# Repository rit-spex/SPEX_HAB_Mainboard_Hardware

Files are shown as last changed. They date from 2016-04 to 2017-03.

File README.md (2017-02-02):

# SPEX_HAB_Mainboard_Hardware

Mainboard for RIT SPEX's High Altitude Balloon Program. 
This board is part of a modular system that allows for quick reuse and testing of future cubesat payloads.

Hardware on board includes:
- Altimeter
- 9DOF IMU
- Temperature Sensor
- Three external Thermistors
- Onboard MicroSD Storage 
- MOSFETs for multiple voltages
- Full Dataline ESD Protection

   
 

   



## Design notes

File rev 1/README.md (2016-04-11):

# SPEX_HAB_Mainboard_Hardware

Mainboard for RIT SPEX's High Altitude Balloon Program. 
This board is part of a modular system that allows for quick reuse and testing of future cubesat payloads.

Hardware on board includes:
- Altimeter
- 9DOF IMU
- Temperature Sensor
- Three external Thermistors
- 64Mbit of Flash Storage
- Onboard MicroSD Storage 
- Relays and MOSFETs for multiple voltages
- Full Dataline ESD Protection

   
 

   



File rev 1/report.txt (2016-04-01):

Info: Reading netlist file "C:\Users\matthew\Desktop\SPEX-Mainboard-Hardware\Spex-Mainboard-Hardware.net".

Info: Using references to match components and footprints.

Info: Checking netlist component footprint "C1:/5657EA84:Capacitors_SMD:C_0603".

Adding new component "C1:/5657EA84" footprint "Capacitors_SMD:C_0603".

Changing component "C1:/5657EA84" pin "1" net name from "" to "+3V3".

Changing component "C1:/5657EA84" pin "2" net name from "" to "GND".

Info: Checking netlist component footprint "C2:/5657EA4F:Capacitors_SMD:C_0603".

Adding new component "C2:/5657EA4F" footprint "Capacitors_SMD:C_0603".

Changing component "C2:/5657EA4F" pin "1" net name from "" to "+3V3".

Changing component "C2:/5657EA4F" pin "2" net name from "" to "GND".

Info: Checking netlist component footprint "C3:/5657C82F:Capacitors_SMD:C_0603".

Adding new component "C3:/5657C82F" footprint "Capacitors_SMD:C_0603".

Changing component "C3:/5657C82F" pin "1" net name from "" to "+3V3".

Changing component "C3:/5657C82F" pin "2" net name from "" to "GND".

Info: Checking netlist component footprint "C4:/5657C7F2:Capacitors_SMD:C_0603".

Adding new component "C4:/5657C7F2" footprint "Capacitors_SMD:C_0603".

Changing component "C4:/5657C7F2" pin "1" net name from "" to "+3V3".

Changing component "C4:/5657C7F2" pin "2" net name from "" to "GND".

Info: Checking netlist component footprint "C5:/5700DE6B:Capacitors_SMD:C_0603".

Adding new component "C5:/5700DE6B" footprint "Capacitors_SMD:C_0603".

Changing component "C5:/5700DE6B" pin "1" net name from "" to "+3V3".

Changing component "C5:/5700DE6B" pin "2" net name from "" to "GND".

Info: Checking netlist component footprint "C6:/56FA860A:Capacitors_SMD:C_0603".

Adding new component "C6:/56FA860A" footprint "Capacitors_SMD:C_0603".

Changing component "C6:/56FA860A" pin "1" net name from "" to "Net-(C6-Pad1)".

Changing component "C6:/56FA860A" pin "2" net name from "" to "GND".

Info: Checking netlist component footprint "C7:/5679E0BF:Capacitors_SMD:C_0603".

Adding new component "C7:/5679E0BF" footprint "Capacitors_SMD:C_0603".

Changing component "C7:/5679E0BF" pin "1" net name from "" to "Net-(C7-Pad1)".

Changing component "C7:/5679E0BF" pin "2" net name from "" to "GND".

Info: Checking netlist component footprint "C8:/5679E124:Capacitors_SMD:C_0603".

Adding new component "C8:/5679E124" footprint "Capacitors_SMD:C_0603".

Changing component "C8:/5679E124" pin "1" net name from "" to "Net-(C8-Pad1)".

Changing component "C8:/5679E124" pin "2" net name from "" to "GND".

Info: Checking netlist component footprint "C9:/56DF35A9/56DF43E0:Capacitors_SMD:C_0603".

Adding new component "C9:/56DF35A9/56DF43E0" footprint "Capacitors_SMD:C_0603".

Changing component "C9:/56DF35A9/56DF43E0" pin "1" net name from "" to "Net-(C9-Pad1)".

Changing component "C9:/56DF35A9/56DF43E0" pin "2" net name from "" to "GND".

Info: Checking netlist component footprint "C10:/56DF35A9/56DF438F:Capacitors_SMD:C_0603".

Adding new component "C10:/56DF35A9/56DF438F" footprint "Capacitors_SMD:C_0603".

Changing component "C10:/56DF35A9/56DF438F" pin "1" net name from "" to "+3V3".

Changing component "C10:/56DF35A9/56DF438F" pin "2" net name from "" to "GND".

Info: Checking netlist component footprint "C11:/56DF35A9/56DF6921:Capacitors_SMD:C_0603".

Adding new component "C11:/56DF35A9/56DF6921" footprint "Capacitors_SMD:C_0603".

Changing component "C11:/56DF35A9/56DF6921" pin "1" net name from "" to "+3V3".

Changing component "C11:/56DF35A9/56DF6921" pin "2" net name from "" to "GND".

Info: Checking netlist component footprint "C12:/56DF35A9/56DF6AFC:Capacitors_SMD:C_0603".

Adding new component "C12:/56DF35A9/56DF6AFC" footprint "Capacitors_SMD:C_0603".

Changing component "C12:/56DF35A9/56DF6AFC" pin "1" net name from "" to "Net-(C12-Pad1)".

Changing component "C12:/56DF35A9/56DF6AFC" pin "2" net name from "" to "GND".

Info: Checking netlist component footprint "C13:/56DF35A9/56DF6B56:Capacitors_SMD:C_0603".

Adding new component "C13:/56DF35A9/56DF6B56" footprint "Capacitors_SMD:C_0603".

Changing component "C13:/56DF35A9/56DF6B56" pin "1" net name from "" to "Net-(C13-Pad1)".

Changing component "C13:/56DF35A9/56DF6B56" pin "2" net name from "" to "GND".

Info: Checking netlist component footprint "C14:/56DF35A9/56E7C20E:Capacitors_SMD:C_0603".

Adding new component "C14:/56DF35A9/56E7C20E" footprint "Capacitors_SMD:C_0603".

Changing component "C14:/56DF35A9/56E7C20E" pin "1" net name from "" to "/HAB Sensors/2.5VRefVoltage".

Changing component "C14:/56DF35A9/56E7C20E" pin "2" net name from "" to "GND".

Info: Checking netlist component footprint "C15:/56DF35A9/56DF6C79:Capacitors_SMD:C_0603".

Adding new component "C15:/56DF35A9/56DF6C79" footprint "Capacitors_SMD:C_0603".

Changing component "C15:/56DF35A9/56DF6C79" pin "1" net name from "" to "+3V3".

Changing component "C15:/56DF35A9/56DF6C79" pin "2" net name from "" to "GND".

Info: Checking netlist component footprint "C16:/56DF35A9/56DF6DC2:Capacitors_SMD:C_0603".

Adding new component "C16:/56DF35A9/56DF6DC2" footprint "Capacitors_SMD:C_0603".

Changing component "C16:/56DF35A9/56DF6DC2" pin "1" net name from "" to "+3V3".

Changing component "C16:/56DF35A9/56DF6DC2" pin "2" net name from "" to "GND".

Info: Checking netlist component footprint "C17:/56EB0DA0/56EC0199:Capacitors_SMD:C_0603".

Adding new component "C17:/56EB0DA0/56EC0199" footprint "Capacitors_SMD:C_0603".

Changing component "C17:/56EB0DA0/56EC0199" pin "1" net name from "" to "+3V3".

Changing component "C17:/56EB0DA0/56EC0199" pin "2" net name from "" to "GND".

Info: Checking netlist component footprint "C18:/56EB0DA0/56EB2C07:Capacitors_SMD:C_0603".

Adding new component "C18:/56EB0DA0/56EB2C07" footprint "Capacitors_SMD:C_0603".

Changing component "C18:/56EB0DA0/56EB2C07" pin "1" net name from "" to "+3V3".

Changing component "C18:/56EB0DA0/56EB2C07" pin "2" net name from "" to "GND".

Info: Checking netlist component footprint "C19:/56EB0DA0/56F4339B:Capacitors_SMD:C_0603".

Adding new component "C19:/56EB0DA0/56F4339B" footprint "Capacitors_SMD:C_0603".

Changing component "C19:/56EB0DA0/56F4339B" pin "1" net name from "" to "+3V3".

Changing component "C19:/56EB0DA0/56F4339B" pin "2" net name from "" to "GND".

Info: Checking netlist component footprint "C20:/56EB0DA0/56F433E0:Capacitors_SMD:C_0603".

Adding new component "C20:/56EB0DA0/56F433E0" footprint "Capacitors_SMD:C_0603".

Changing component "C20:/56EB0DA0/56F433E0" pin "1" net name from "" to "+3V3".

Changing component "C20:/56EB0DA0/56F433E0" pin "2" net name from "" to "GND".

Info: Checking netlist component footprint "C21:/56FB76C9:Capacitors_SMD:C_0603".

Adding new component "C21:/56FB76C9" footprint "Capacitors_SMD:C_0603".

Changing component "C21:/56FB76C9" pin "1" net name from "" to "+3V3".

Changing component "C21:/56FB76C9" pin "2" net name from "" to "GND".

Info: Checking netlist component footprint "D1:/56DC1E42:LEDs:LED_0603".

Adding new component "D1:/56DC1E42" footprint "LEDs:LED_0603".

Changing component "D1:/56DC1E42" pin "2" net name from "" to "Net-(D1-Pad2)".

Changing component "D1:/56DC1E42" pin "1" net name from "" to "GND".

Info: Checking netlist component footprint "D2:/56ECA2DA:LEDs:LED_0603".

Adding new component "D2:/56ECA2DA" footprint "LEDs:LED_0603".

Changing component "D2:/56ECA2DA" pin "2" net name from "" to "Net-(D2-Pad2)".

Changing component "D2:/56ECA2DA" pin "1" net name from "" to "GND".

Info: Checking netlist component footprint "D3:/56ECA423:LEDs:LED_0603".

Adding new component "D3:/56ECA423" footprint "LEDs:LED_0603".

Changing component "D3:/56ECA423" pin "2" net name from "" to "Net-(D3-Pad2)".

Changing component "D3:/56ECA423" pin "1" net name from "" to "GND".

Info: Checking netlist component footprint "D4:/56ECA578:LEDs:LED_0603".

Adding new component "D4:/56ECA578" footprint "LEDs:LED_0603".

Changing component "D4:/56ECA578" pin "2" net name from "" to "Net-(D4-Pad2)".

Changing component "D4:/56ECA578" pin "1" net name from "" to "GND".

Info: Checking netlist component footprint "D5:/56EB0DA0/56F8595E:Diodes_SMD:SMA_Standard".

Adding new component "D5:/56EB0DA0/56F8595E" footprint "Diodes_SMD:SMA_Standard".

Changing component "D5:/56EB0DA0/56F8595E" pin "1" net name from "" to "+3V3".

Changing component "D5:/56EB0DA0/56F8595E" pin "2" net name from "" to "Net-(D5-Pad2)".

Info: Checking netlist component footprint "D6:/56EB0DA0/56F85A58:Diodes_SMD:SMA_Standard".

Adding new component "D6:/56EB0DA0/56F85A58" footprint "Diodes_SMD:SMA_Standard".

Changing component "D6:/56EB0DA0/56F85A58" pin "1" net name from "" to "+3V3".

Changing component "D6:/56EB0DA0/56F85A58" pin "2" net name from "" to "Net-(D6-Pad2)".

Info: Checking netlist component footprint "K1:/56EB0DA0/56F71C9B:SPEX_Parts:G5LE-1A4-DC3".

Adding new component "K1:/56EB0DA0/56F71C9B" footprint "SPEX_Parts:G5LE-1A4-DC3".

Changing component "K1:/56EB0DA0/56F71C9B" pin "2" net name from "" to "Net-(D5-Pad2)".

Changing component "K1:/56EB0DA0/56F71C9B" pin "3" net name from "" to "/Data_Input_Output/Battery_Out".

Changing component "K1:/56EB0DA0/56F71C9B" pin "4" net name from "" to "+3V3".

Info: Checking netlist component footprint "K2:/56EB0DA0/56F71C01:SPEX_Parts:G5LE-1A4-DC3".

Adding new component "K2:/56EB0DA0/56F71C01" footprint "SPEX_Parts:G5LE-1A4-DC3".

Changing component "K2:/56EB0DA0/56F71C01" pin "2" net name from "" to "Net-(D6-Pad2)".

Changing component "K2:/56EB0DA0/56F71C01" pin "3" net name from "" to "/Data_Input_Output/User_Out".

Changing component "K2:/56EB0DA0/56F71C01" pin "4" net name from "" to "+3V3".

Info: Checking netlist component footprint "P1:/56581306:Connect:USB_Micro-B".

Adding new component "P1:/56581306" footprint "Connect:USB_Micro-B".

Changing component "P1:/56581306" pin "1" net name from "" to "Net-(P1-Pad1)".

Changing component "P1:/56581306" pin "2" net name from "" to "Net-(P1-Pad2)".

Changing component "P1:/56581306" pin "3" net name from "" to "Net-(P1-Pad3)".

Changing component "P1:/56581306" pin "4" net name from "" to "/PTA6".

Changing component "P1:/56581306" pin "5" net name from "" to "GND".

Changing component "P1:/56581306" pin "6" net name from "" to "GND".

Changing component "P1:/56581306" pin "6" net name from "" to "GND".

Changing component "P1:/56581306" pin "6" net name from "" to "GND".

Changing component "P1:/56581306" pin "6" net name from "" to "GND".

Info: Checking netlist component footprint "P2:/56792B34:SPEX_Parts:SWD-10".

Adding new component "P2:/56792B34" footprint "SPEX_Parts:SWD-10".

Changing component "P2:/56792B34" pin "10" net name from "" to "/RESET_b".

Changing component "P2:/56792B34" pin "1" net name from "" to "+3V3".

Changing component "P2:/56792B34" pin "9" net name from "" to "Net-(P2-Pad9)".

Changing component "P2:/56792B34" pin "2" net name from "" to "/PTA7".

Changing component "P2:/56792B34" pin "8" net name from "" to "Net-(P2-Pad8)".

Changing component "P2:/56792B34" pin "3" net name from "" to "GND".

Changing component "P2:/56792B34" pin "7" net name from "" to "Net-(P2-Pad7)".

Changing component "P2:/56792B34" pin "4" net name from "" to "/PTB0".

Changing component "P2:/56792B34" pin "6" net name from "" to "Net-(P2-Pad6)".

Changing component "P2:/56792B34" pin "5" net name from "" to "GND".

Info: Checking netlist component footprint "Q1:/56EB0DA0/56F71D8D:TO_SOT_Packages_SMD:SOT-23".

Adding new component "Q1:/56EB0DA0/56F71D8D" footprint "TO_SOT_Packages_SMD:SOT-23".

Changing component "Q1:/56EB0DA0/56F71D8D" pin "1" net name from "" to "Relay1_ctrl".

Changing component "Q1:/56EB0DA0/56F71D8D" pin "2" net name from "" to "GND".

Changing component "Q1:/56EB0DA0/56F71D8D" pin "3" net name from "" to "Net-(D5-Pad2)".

Info: Checking netlist component footprint "Q2:/56EB0DA0/56F71D09:TO_SOT_Packages_SMD:SOT-23".

Adding new component "Q2:/56EB0DA0/56F71D09" footprint "TO_SOT_Packages_SMD:SOT-23".

Changing component "Q2:/56EB0DA0/56F71D09" pin "1" net name from "" to "Relay2_ctrl".

Changing component "Q2:/56EB0DA0/56F71D09" pin "2" net name from "" to "GND".

Changing component "Q2:/56EB0DA0/56F71D09" pin "3" net name from "" to "Net-(D6-Pad2)".

Info: Checking netlist component footprint "Q3:/56EB0DA0/56F63DDC:TO_SOT_Packages_SMD:SOT-23".

Adding new component "Q3:/56EB0DA0/56F63DDC" footprint "TO_SOT_Packages_SMD:SOT-23".

Changing component "Q3:/56EB0DA0/56F63DDC" pin "1" net name from "" to "SD_CTRL".

Changing component "Q3:/56EB0DA0/56F63DDC" pin "2" net name from "" to "+3V3".

Changing component "Q3:/56EB0DA0/56F63DDC" pin "3" net name from "" to "Net-(Q3-Pad3)".

Info: Checking netlist component footprint "Q4:/56EB0DA0/56F6A63A:SPEX_Parts:ChipFet-8".

Adding new component "Q4:/56EB0DA0/56F6A63A" footprint "SPEX_Parts:ChipFet-8".

Changing component "Q4:/56EB0DA0/56F6A63A" pin "8" net name from "" to "/Data_Input_Output/3.3V_MOS_OUT".

Changing component "Q4:/56EB0DA0/56F6A63A" pin "1" net name from "" to "/Data_Input_Output/3.3V_MOS_OUT".

Changing component "Q4:/56EB0DA0/56F6A63A" pin "7" net name from "" to "/Data_Input_Output/3.3V_MOS_OUT".

Changing component "Q4:/56EB0DA0/56F6A63A" pin "2" net name from "" to "/Data_Input_Output/3.3V_MOS_OUT".

Changing component "Q4:/56EB0DA0/56F6A63A" pin "6" net name from "" to "/Data_Input_Output/3.3V_MOS_OUT".

Changing component "Q4:/56EB0DA0/56F6A63A" pin "3" net name from "" to "/Data_Input_Output/3.3V_MOS_OUT".

Changing component "Q4:/56EB0DA0/56F6A63A" pin "5" net name from "" to "GND".

Changing component "Q4:/56EB0DA0/56F6A63A" pin "4" net name from "" to "3.3V_MOS_CTRL".

Info: Checking netlist component footprint "Q5:/56EB0DA0/56F6A694:SPEX_Parts:ChipFet-8".

Adding new component "Q5:/56EB0DA0/56F6A694" footprint "SPEX_Parts:ChipFet-8".

Changing component "Q5:/56EB0DA0/56F6A694" pin "8" net name from "" to "/Data_Input_Output/5V_MOS_OUT".

Changing component "Q5:/56EB0DA0/56F6A694" pin "1" net name from "" to "/Data_Input_Output/5V_MOS_OUT".

Changing component "Q5:/56EB0DA0/56F6A694" pin "7" net name from "" to "/Data_Input_Output/5V_MOS_OUT".

Changing component "Q5:/56EB0DA0/56F6A694" pin "2" net name from "" to "/Data_Input_Output/5V_MOS_OUT".

Changing component "Q5:/56EB0DA0/56F6A694" pin "6" net name from "" to "/Data_Input_Output/5V_MOS_OUT".

Changing component "Q5:/56EB0DA0/56F6A694" pin "3" net name from "" to "/Data_Input_Output/5V_MOS_OUT".

Changing component "Q5:/56EB0DA0/56F6A694" pin "5" net name from "" to "GND".

Changing component "Q5:/56EB0DA0/56F6A694" pin "4" net name from "" to "5V_MOS_CTRL".

Info: Checking netlist component footprint "Q6:/56EB0DA0/56F6A6EC:SPEX_Parts:ChipFet-8".

Adding new component "Q6:/56EB0DA0/56F6A6EC" footprint "SPEX_Parts:ChipFet-8".

Changing component "Q6:/56EB0DA0/56F6A6EC" pin "8" net name from "" to "/Data_Input_Output/Vbus_MOS_OUT".

Changing component "Q6:/56EB0DA0/56F6A6EC" pin "1" net name from "" to "/Data_Input_Output/Vbus_MOS_OUT".

Changing component "Q6:/56EB0DA0/56F6A6EC" pin "7" net name from "" to "/Data_Input_Output/Vbus_MOS_OUT".

Changing component "Q6:/56EB0DA0/56F6A6EC" pin "2" net name from "" to "/Data_Input_Output/Vbus_MOS_OUT".

Changing component "Q6:/56EB0DA0/56F6A6EC" pin "6" net name from "" to "/Data_Input_Output/Vbus_MOS_OUT".

Changing component "Q6:/56EB0DA0/56F6A6EC" pin "3" net name from "" to "/Data_Input_Output/Vbus_MOS_OUT".

Changing component "Q6:/56EB0DA0/56F6A6EC" pin "5" net name from "" to "GND".

Changing component "Q6:/56EB0DA0/56F6A6EC" pin "4" net name from "" to "Vbus_MOS_CTRL".

Info: Checking netlist component footprint "R1:/56DC1F46:Resistors_SMD:R_0603".

Adding new component "R1:/56DC1F46" footprint "Resistors_SMD:R_0603".

Changing component "R1:/56DC1F46" pin "1" net name from "" to "Net-(P1-Pad1)".

Changing component "R1:/56DC1F46" pin "2" net name from "" to "Net-(D1-Pad2)".

Info: Checking netlist component footprint "R2:/56DEC86B:Resistors_SMD:R_0603".

Adding new component "R2:/56DEC86B" footprint "Resistors_SMD:R_0603".

Changing component "R2:/56DEC86B" pin "1" net name from "" to "Net-(R2-Pad1)".

Changing component "R2:/56DEC86B" pin "2" net name from "" to "Net-(P1-Pad1)".

Info: Checking netlist component footprint "R3:/5678C3E0:Resistors_SMD:R_0603".

Adding new component "R3:/5678C3E0" footprint "Resistors_SMD:R_0603".

Changing component "R3:/5678C3E0" pin "1" net name from "" to "Net-(R3-Pad1)".

Changing component "R3:/5678C3E0" pin "2" net name from "" to "Net-(P1-Pad3)".

Info: Checking netlist component footprint "R4:/5678C441:Resistors_SMD:R_0603".

Adding new component "R4:/5678C441" footprint "Resistors_SMD:R_0603".

Changing component "R4:/5678C441" pin "1" net name from "" to "Net-(R4-Pad1)".

Changing component "R4:/5678C441" pin "2" net name from "" to "Net-(P1-Pad2)".

Info: Checking netlist component footprint "R5:/56FF52C8:Resistors_SMD:R_0603".

Adding new component "R5:/56FF52C8" footprint "Resistors_SMD:R_0603".

Changing component "R5:/56FF52C8" pin "1" net name from "" to "I2C1_SDA".

Changing component "R5:/56FF52C8" pin "2" net name from "" to "+3V3".

Info: Checking netlist component footprint "R6:/56FF52CE:Resistors_SMD:R_0603".

Adding new component "R6:/56FF52CE" footprint "Resistors_SMD:R_0603".

Changing component "R6:/56FF52CE" pin "1" net name from "" to "I2C1_SCL".

Changing component "R6:/56FF52CE" pin "2" net name from "" to "+3V3".

Info: Checking netlist component footprint "R7:/5657C74F:Resistors_SMD:R_0603".

Adding new component "R7:/5657C74F" footprint "Resistors_SMD:R_0603".

Changing component "R7:/5657C74F" pin "1" net name from "" to "I2C0_SDA".

Changing component "R7:/5657C74F" pin "2" net name from "" to "+3V3".

Info: Checking netlist component footprint "R8:/5657C78A:Resistors_SMD:R_0603".

Adding new component "R8:/5657C78A" footprint "Resistors_SMD:R_0603".

Changing component "R8:/5657C78A" pin "1" net name from "" to "I2C0_SCL".

Changing component "R8:/5657C78A" pin "2" net name from "" to "+3V3".

Info: Checking netlist component footprint "R9:/56EC9EE5:Resistors_SMD:R_0603".

Adding new component "R9:/56EC9EE5" footprint "Resistors_SMD:R_0603".

Changing component "R9:/56EC9EE5" pin "1" net name from "" to "LED_Heartbeat".

Changing component "R9:/56EC9EE5" pin "2" net name from "" to "Net-(D2-Pad2)".

Info: Checking netlist component footprint "R10:/56ECA026:Resistors_SMD:R_0603".

Adding new component "R10:/56ECA026" footprint "Resistors_SMD:R_0603".

Changing component "R10:/56ECA026" pin "1" net name from "" to "LED_Status_1".

Changing component "R10:/56ECA026" pin "2" net name from "" to "Net-(D3-Pad2)".

Info: Checking netlist component footprint "R11:/56ECA17D:Resistors_SMD:R_0603".

Adding new component "R11:/56ECA17D" footprint "Resistors_SMD:R_0603".

Changing component "R11:/56ECA17D" pin "1" net name from "" to "LED_Status_2".

Changing component "R11:/56ECA17D" pin "2" net name from "" to "Net-(D4-Pad2)".

Info: Checking netlist component footprint "R12:/56DEC23C:Resistors_SMD:R_0603".

Adding new component "R12:/56DEC23C" footprint "Resistors_SMD:R_0603".

Changing component "R12:/56DEC23C" pin "1" net name from "" to "+3V3".

Changing component "R12:/56DEC23C" pin "2" net name from "" to "Net-(R12-Pad2)".

Info: Checking netlist component footprint "R13:/56DEC45A:Resistors_SMD:R_0603".

Adding new component "R13:/56DEC45A" footprint "Resistors_SMD:R_0603".

Changing component "R13:/56DEC45A" pin "1" net name from "" to "+3V3".

Changing component "R13:/56DEC45A" pin "2" net name from "" to "Net-(R13-Pad2)".

Info: Checking netlist component footprint "R14:/56DF35A9/56E7CA04:Resistors_SMD:R_0603".

Adding new component "R14:/56DF35A9/56E7CA04" footprint "Resistors_SMD:R_0603".

Changing component "R14:/56DF35A9/56E7CA04" pin "1" net name from "" to "Temp1".

Changing component "R14:/56DF35A9/56E7CA04" pin "2" net name from "" to "GND".

Info: Checking netlist component footprint "R15:/56DF35A9/56F543EA:Resistors_SMD:R_0603".

Adding new component "R15:/56DF35A9/56F543EA" footprint "Resistors_SMD:R_0603".

Changing component "R15:/56DF35A9/56F543EA" pin "1" net name from "" to "Temp2".

Changing component "R15:/56DF35A9/56F543EA" pin "2" net name from "" to "GND".

Info: Checking netlist component footprint "R16:/56DF35A9/56E7CABB:Resistors_SMD:R_0603".

Adding new component "R16:/56DF35A9/56E7CABB" footprint "Resistors_SMD:R_0603".

Changing component "R16:/56DF35A9/56E7CABB" pin "1" net name from "" to "Temp3".

Changing component "R16:/56DF35A9/56E7CABB" pin "2" net name from "" to "GND".

Info: Checking netlist component footprint "R17:/56DF35A9/56E7C1A7:Resistors_SMD:R_0603".

Adding new component "R17:/56DF35A9/56E7C1A7" footprint "Resistors_SMD:R_0603".

Changing component "R17:/56DF35A9/56E7C1A7" pin "1" net name from "" to "+3V3".

Changing component "R17:/56DF35A9/56E7C1A7" pin "2" net name from "" to "/HAB Sensors/2.5VRefVoltage".

Info: Checking netlist component footprint "R18:/56DF75A2/56DE6203:Resistors_SMD:R_0603".

Adding new component "R18:/56DF75A2/56DE6203" footprint "Resistors_SMD:R_0603".

Changing component "R18:/56DF75A2/56DE6203" pin "1" net name from "" to "Net-(R18-Pad1)".

Changing component "R18:/56DF75A2/56DE6203" pin "2" net name from "" to "/Power Distribution/VBus".

Info: Checking netlist component footprint "R19:/56DF75A2/56DE621B:Resistors_SMD:R_0603".

Adding new component "R19:/56DF75A2/56DE621B" footprint "Resistors_SMD:R_0603".

Changing component "R19:/56DF75A2/56DE621B" pin "1" net name from "" to "Net-(R19-Pad1)".

Changing component "R19:/56DF75A2/56DE621B" pin "2" net name from "" to "VBatt".

Info: Checking netlist component footprint "R20:/56DF75A2/56DE6236:Resistors_SMD:R_0603".

Adding new component "R20:/56DF75A2/56DE6236" footprint "Resistors_SMD:R_0603".

Changing component "R20:/56DF75A2/56DE6236" pin "1" net name from "" to "Net-(R20-Pad1)".

Changing component "R20:/56DF75A2/56DE6236" pin "2" net name from "" to "/Power Distribution/Bat1-2".

Info: Checking netlist component footprint "R21:/56DF75A2/56DE6251:Resistors_SMD:R_0603".

Adding new component "R21:/56DF75A2/56DE6251" footprint "Resistors_SMD:R_0603".

Changing component "R21:/56DF75A2/56DE6251" pin "1" net name from "" to "Net-(R21-Pad1)".

Changing component "R21:/56DF75A2/56DE6251" pin "2" net name from "" to "/Power Distribution/Bat2-3".

Info: Checking netlist component footprint "R22:/56DF75A2/56DE626E:Resistors_SMD:R_0603".

Adding new component "R22:/56DF75A2/56DE626E" footprint "Resistors_SMD:R_0603".

Changing component "R22:/56DF75A2/56DE626E" pin "1" net name from "" to "Net-(R22-Pad1)".

Changing component "R22:/56DF75A2/56DE626E" pin "2" net name from "" to "/Power Distribution/BatGnd".

Info: Checking netlist component footprint "R23:/56DF75A2/56DE6291:Resistors_SMD:R_0603".

Adding new component "R23:/56DF75A2/56DE6291" footprint "Resistors_SMD:R_0603".

Changing component "R23:/56DF75A2/56DE6291" pin "1" net name from "" to "Net-(R23-Pad1)".

Changing component "R23:/56DF75A2/56DE6291" pin "2" net name from "" to "I2C0_SDA".

Info: Checking netlist component footprint "R24:/56DF75A2/56DE62B4:Resistors_SMD:R_0603".

Adding new component "R24:/56DF75A2/56DE62B4" footprint "Resistors_SMD:R_0603".

Changing component "R24:/56DF75A2/56DE62B4" pin "1" net name from "" to "Net-(R24-Pad1)".

Changing component "R24:/56DF75A2/56DE62B4" pin "2" net name from "" to "I2C0_SCL".

Info: Checking netlist component footprint "R25:/56DF75A2/56DE62DB:Resistors_SMD:R_0603".

Adding new component "R25:/56DF75A2/56DE62DB" footprint "Resistors_SMD:R_0603".

Changing component "R25:/56DF75A2/56DE62DB" pin "1" net name from "" to "Net-(R25-Pad1)".

Changing component "R25:/56DF75A2/56DE62DB" pin "2" net name from "" to "/Power Distribution/PowIRQ".

Info: Checking netlist component footprint "R26:/56DF75A2/56DE6304:Resistors_SMD:R_0603".

Adding new component "R26:/56DF75A2/56DE6304" footprint "Resistors_SMD:R_0603".

Changing component "R26:/56DF75A2/56DE6304" pin "1" net name from "" to "Net-(R26-Pad1)".

Changing component "R26:/56DF75A2/56DE6304" pin "2" net name from "" to "+3V3".

Info: Checking netlist component footprint "R27:/56DF75A2/56DE632D:Resistors_SMD:R_0603".

Adding new component "R27:/56DF75A2/56DE632D" footprint "Resistors_SMD:R_0603".

Changing component "R27:/56DF75A2/56DE632D" pin "1" net name from "" to "Net-(R27-Pad1)".

Changing component "R27:/56DF75A2/56DE632D" pin "2" net name from "" to "GND".

Info: Checking netlist component footprint "R28:/56EB0DA0/56EC0138:Resistors_SMD:R_0603".

Adding new component "R28:/56EB0DA0/56EC0138" footprint "Resistors_SMD:R_0603".

Changing component "R28:/56EB0DA0/56EC0138" pin "1" net name from "" to "Net-(R28-Pad1)".

Changing component "R28:/56EB0DA0/56EC0138" pin "2" net name from "" to "GND".

Info: Checking netlist component footprint "R29:/56EB0DA0/56F7836B:Resistors_SMD:R_0603".

Adding new component "R29:/56EB0DA0/56F7836B" footprint "Resistors_SMD:R_0603".

Changing component "R29:/56EB0DA0/56F7836B" pin "1" net name from "" to "Relay1_ctrl".

Changing component "R29:/56EB0DA0/56F7836B" pin "2" net name from "" to "GND".

Info: Checking netlist component footprint "R30:/56EB0DA0/56EB28B1:Resistors_SMD:R_0603".

Adding new component "R30:/56EB0DA0/56EB28B1" footprint "Resistors_SMD:R_0603".

Changing component "R30:/56EB0DA0/56EB28B1" pin "1" net name from "" to "+3V3".

Changing component "R30:/56EB0DA0/56EB28B1" pin "2" net name from "" to "/Data_Input_Output/RS485_B".

Info: Checking netlist component footprint "R31:/56EB0DA0/56EB28FE:Resistors_SMD:R_0603".

Adding new component "R31:/56EB0DA0/56EB28FE" footprint "Resistors_SMD:R_0603".

Changing component "R31:/56EB0DA0/56EB28FE" pin "1" net name from "" to "/Data_Input_Output/RS485_A".

Changing component "R31:/56EB0DA0/56EB28FE" pin "2" net name from "" to "GND".

Info: Checking netlist component footprint "R32:/56EB0DA0/56EC08CE:Resistors_SMD:R_0603".

Adding new component "R32:/56EB0DA0/56EC08CE" footprint "Resistors_SMD:R_0603".

Changing component "R32:/56EB0DA0/56EC08CE" pin "1" net name from "" to "/Data_Input_Output/CANH_out".

Changing component "R32:/56EB0DA0/56EC08CE" pin "2" net name from "" to "/Data_Input_Output/CANL_out".

Info: Checking netlist component footprint "R33:/56EB0DA0/56EB22CF:Resistors_SMD:R_0603".

Adding new component "R33:/56EB0DA0/56EB22CF" footprint "Resistors_SMD:R_0603".

Changing component "R33:/56EB0DA0/56EB22CF" pin "1" net name from "" to "/Data_Input_Output/RS485_B".

Changing component "R33:/56EB0DA0/56EB22CF" pin "2" net name from "" to "/Data_Input_Output/RS485_A".

Info: Checking netlist component footprint "R34:/56EB0DA0/56F78404:Resistors_SMD:R_0603".

Adding new component "R34:/56EB0DA0/56F78404" footprint "Resistors_SMD:R_0603".

Changing component "R34:/56EB0DA0/56F78404" pin "1" net name from "" to "Relay2_ctrl".

Changing component "R34:/56EB0DA0/56F78404" pin "2" net name from "" to "GND".

Info: Checking netlist component footprint "R35:/56EB0DA0/56ED5F75:Resistors_SMD:R_0603".

Adding new component "R35:/56EB0DA0/56ED5F75" footprint "Resistors_SMD:R_0603".

Changing component "R35:/56EB0DA0/56ED5F75" pin "1" net name from "" to "GND".

Changing component "R35:/56EB0DA0/56ED5F75" pin "2" net name from "" to "3.3V_MOS_CTRL".

Info: Checking netlist component footprint "R36:/56EB0DA0/56ED6EC5:Resistors_SMD:R_0603".

Adding new component "R36:/56EB0DA0/56ED6EC5" footprint "Resistors_SMD:R_0603".

Changing component "R36:/56EB0DA0/56ED6EC5" pin "1" net name from "" to "GND".

Changing component "R36:/56EB0DA0/56ED6EC5" pin "2" net name from "" to "5V_MOS_CTRL".

Info: Checking netlist component footprint "R37:/56EB0DA0/56ED7325:Resistors_SMD:R_0603".

Adding new component "R37:/56EB0DA0/56ED7325" footprint "Resistors_SMD:R_0603".

Changing component "R37:/56EB0DA0/56ED7325" pin "1" net name from "" to "GND".

Changing component "R37:/56EB0DA0/56ED7325" pin "2" net name from "" to "Vbus_MOS_CTRL".

Info: Checking netlist component footprint "R38:/56EB0DA0/56F64360:Resistors_SMD:R_0603".

Adding new component "R38:/56EB0DA0/56F64360" footprint "Resistors_SMD:R_0603".

Changing component "R38:/56EB0DA0/56F64360" pin "1" net name from "" to "SD_CTRL".

Changing component "R38:/56EB0DA0/56F64360" pin "2" net name from "" to "+3V3".

Info: Checking netlist component footprint "SW1:/56DF1158:Buttons_Switches_SMD:SW_SPST_B3S-1000".

Adding new component "SW1:/56DF1158" footprint "Buttons_Switches_SMD:SW_SPST_B3S-1000".

Changing component "SW1:/56DF1158" pin "1" net name from "" to "/PTB2".

Changing component "SW1:/56DF1158" pin "1" net name from "" to "/PTB2".

Changing component "SW1:/56DF1158" pin "2" net name from "" to "GND".

Changing component "SW1:/56DF1158" pin "2" net name from "" to "GND".

Info: Checking netlist component footprint "TH1:/56DF35A9/56E7C90A:Connect:PINHEAD1-2".

Adding new component "TH1:/56DF35A9/56E7C90A" footprint "Connect:PINHEAD1-2".

Changing component "TH1:/56DF35A9/56E7C90A" pin "1" net name from "" to "/HAB Sensors/2.5VRefVoltage".

Changing component "TH1:/56DF35A9/56E7C90A" pin "2" net name from "" to "Temp1".

Info: Checking netlist component footprint "TH2:/56DF35A9/56E7C985:Connect:PINHEAD1-2".

Adding new component "TH2:/56DF35A9/56E7C985" footprint "Connect:PINHEAD1-2".

Changing component "TH2:/56DF35A9/56E7C985" pin "1" net name from "" to "/HAB Sensors/2.5VRefVoltage".

Changing component "TH2:/56DF35A9/56E7C985" pin "2" net name from "" to "Temp2".

Info: Checking netlist component footprint "TH3:/56DF35A9/56F54245:Connect:PINHEAD1-2".

Adding new component "TH3:/56DF35A9/56F54245" footprint "Connect:PINHEAD1-2".

Changing component "TH3:/56DF35A9/56F54245" pin "1" net name from "" to "/HAB Sensors/2.5VRefVoltage".

Changing component "TH3:/56DF35A9/56F54245" pin "2" net name from "" to "Temp3".

Info: Checking netlist component footprint "U1:/56F588A7:Housings_QFP:LQFP-32_7x7mm_Pitch0.8mm".

Adding new component "U1:/56F588A7" footprint "Housings_QFP:LQFP-32_7x7mm_Pitch0.8mm".

Changing component "U1:/56F588A7" pin "1" net name from "" to "Net-(U1-Pad1)".

Changing component "U1:/56F588A7" pin "2" net name from "" to "Net-(U1-Pad2)".

Changing component "U1:/56F588A7" pin "3" net name from "" to "+3V3".

Changing component "U1:/56F588A7" pin "4" net name from "" to "+3V3".

Changing component "U1:/56F588A7" pin "5" net name from "" to "GND".

Changing component "U1:/56F588A7" pin "6" net name from "" to "GND".

Changing component "U1:/56F588A7" pin "7" net name from "" to "Net-(U1-Pad7)".

Changing component "U1:/56F588A7" pin "8" net name from "" to "/PTA4".

Changing component "U1:/56F588A7" pin "9" net name from "" to "Net-(U1-Pad9)".

Changing component "U1:/56F588A7" pin "10" net name from "" to "/PTA6".

Changing component "U1:/56F588A7" pin "11" net name from "" to "Net-(U1-Pad11)".

Changing component "U1:/56F588A7" pin "12" net name from "" to "Net-(U1-Pad12)".

Changing component "U1:/56F588A7" pin "13" net name from "" to "Net-(U1-Pad13)".

Changing component "U1:/56F588A7" pin "14" net name from "" to "Net-(U1-Pad14)".

Changing component "U1:/56F588A7" pin "15" net name from "" to "/PTA7".

Changing component "U1:/56F588A7" pin "16" net name from "" to "/PTB0".

Changing component "U1:/56F588A7" pin "17" net name from "" to "/PTB1".

Changing component "U1:/56F588A7" pin "18" net name from "" to "/PTB2".

Changing component "U1:/56F588A7" pin "19" net name from "" to "Net-(U1-Pad19)".

Changing component "U1:/56F588A7" pin "20" net name from "" to "Net-(U1-Pad20)".

Changing component "U1:/56F588A7" pin "21" net name from "" to "Net-(U1-Pad21)".

Changing component "U1:/56F588A7" pin "22" net name from "" to "Net-(U1-Pad22)".

Changing component "U1:/56F588A7" pin "23" net name from "" to "Net-(U1-Pad23)".

Changing component "U1:/56F588A7" pin "24" net name from "" to "Net-(U1-Pad24)".

Changing component "U1:/56F588A7" pin "25" net name from "" to "/PTB5".

Changing component "U1:/56F588A7" pin "26" net name from "" to "Net-(U1-Pad26)".

Changing component "U1:/56F588A7" pin "27" net name from "" to "Net-(U1-Pad27)".

Changing component "U1:/56F588A7" pin "28" net name from "" to "Net-(U1-Pad28)".

Changing component "U1:/56F588A7" pin "29" net name from "" to "Net-(U1-Pad29)".

Changing component "U1:/56F588A7" pin "30" net name from "" to "Net-(U1-Pad30)".

Changing component "U1:/56F588A7" pin "31" net name from "" to "Net-(U1-Pad31)".

Changing component "U1:/56F588A7" pin "32" net name from "" to "Net-(U1-Pad32)".

Info: Checking netlist component footprint "U2:/56DE8990:SPEX_Parts:TSOP-6".

Adding new component "U2:/56DE8990" footprint "SPEX_Parts:TSOP-6".

Changing component "U2:/56DE8990" pin "6" net name from "" to "Net-(P1-Pad2)".

Changing component "U2:/56DE8990" pin "1" net name from "" to "Net-(P1-Pad3)".

Changing component "U2:/56DE8990" pin "5" net name from "" to "Net-(R2-Pad1)".

Changing component "U2:/56DE8990" pin "2" net name from "" to "GND".

Changing component "U2:/56DE8990" pin "4" net name from "" to "Net-(U2-Pad4)".

Changing component "U2:/56DE8990" pin "3" net name from "" to "Net-(U2-Pad3)".

Info: Checking netlist component footprint "U3:/56F352C0:Housings_QFP:LQFP-64_10x10mm_Pitch0.5mm".

Adding new component "U3:/56F352C0" footprint "Housings_QFP:LQFP-64_10x10mm_Pitch0.5mm".

Changing component "U3:/56F352C0" pin "1" net name from "" to "I2C1_SDA".

Changing component "U3:/56F352C0" pin "2" net name from "" to "I2C1_SCL".

Changing component "U3:/56F352C0" pin "3" net name from "" to "+3V3".

Changing component "U3:/56F352C0" pin "4" net name from "" to "GND".

Changing component "U3:/56F352C0" pin "5" net name from "" to "Net-(R3-Pad1)".

Changing component "U3:/56F352C0" pin "6" net name from "" to "Net-(R4-Pad1)".

Changing component "U3:/56F352C0" pin "7" net name from "" to "+3V3".

Changing component "U3:/56F352C0" pin "8" net name from "" to "Net-(U3-Pad8)".

Changing component "U3:/56F352C0" pin "9" net name from "" to "Temp1".

Changing component "U3:/56F352C0" pin "10" net name from "" to "Temp2".

Changing component "U3:/56F352C0" pin "11" net name from "" to "Temp3".

Changing component "U3:/56F352C0" pin "12" net name from "" to "Net-(U3-Pad12)".

Changing component "U3:/56F352C0" pin "13" net name from "" to "+3V3".

Changing component "U3:/56F352C0" pin "14" net name from "" to "+3V3".

Changing component "U3:/56F352C0" pin "15" net name from "" to "GND".

Changing component "U3:/56F352C0" pin "16" net name from "" to "GND".

Changing component "U3:/56F352C0" pin "17" net name from "" to "Net-(C6-Pad1)".

Changing component "U3:/56F352C0" pin "18" net name from "" to "Net-(U3-Pad18)".

Changing component "U3:/56F352C0" pin "19" net name from "" to "Net-(U3-Pad19)".

Changing component "U3:/56F352C0" pin "20" net name from "" to "Net-(U3-Pad20)".

Changing component "U3:/56F352C0" pin "21" net name from "" to "+3V3".

Changing component "U3:/56F352C0" pin "22" net name from "" to "/PTB0".

Changing component "U3:/56F352C0" pin "23" net name from "" to "/PTA6".

Changing component "U3:/56F352C0" pin "24" net name from "" to "/PTB1".

Changing component "U3:/56F352C0" pin "25" net name from "" to "/PTA7".

Changing component "U3:/56F352C0" pin "26" net name from "" to "Net-(U3-Pad26)".

Changing component "U3:/56F352C0" pin "27" net name from "" to "Net-(U3-Pad27)".

Changing component "U3:/56F352C0" pin "28" net name from "" to "CAN0_TX".

Changing component "U3:/56F352C0" pin "29" net name from "" to "CAN0_RX".

Changing component "U3:/56F352C0" pin "30" net name from "" to "+3V3".

Changing component "U3:/56F352C0" pin "31" net name from "" to "GND".

Changing component "U3:/56F352C0" pin "32" net name from "" to "Net-(C7-Pad1)".

Changing component "U3:/56F352C0" pin "33" net name from "" to "Net-(C8-Pad1)".

Changing component "U3:/56F352C0" pin "34" net name from "" to "/PTA4".

Changing component "U3:/56F352C0" pin "35" net name from "" to "Relay2_ctrl".

Changing component "U3:/56F352C0" pin "36" net name from "" to "Relay1_ctrl".

Changing component "U3:/56F352C0" pin "37" net name from "" to "I2C0_SCL".

Changing component "U3:/56F352C0" pin "38" net name from "" to "I2C0_SDA".

Changing component "U3:/56F352C0" pin "39" net name from "" to "UART0_RX".

Changing component "U3:/56F352C0" pin "40" net name from "" to "UART0_TX".

Changing component "U3:/56F352C0" pin "41" net name from "" to "RX/TX_CTRL".

Changing component "U3:/56F352C0" pin "42" net name from "" to "Net-(U3-Pad42)".

Changing component "U3:/56F352C0" pin "43" net name from "" to "Net-(U3-Pad43)".

Changing component "U3:/56F352C0" pin "44" net name from "" to "SD_CTRL".

Changing component "U3:/56F352C0" pin "45" net name from "" to "SD_Detect".

Changing component "U3:/56F352C0" pin "46" net name from "" to "SPI0_CS1".

Changing component "U3:/56F352C0" pin "47" net name from "" to "GND".

Changing component "U3:/56F352C0" pin "48" net name from "" to "+3V3".

Changing component "U3:/56F352C0" pin "49" net name from "" to "SPI0_CS0".

Changing component "U3:/56F352C0" pin "50" net name from "" to "SPI0_SCK".

Changing component "U3:/56F352C0" pin "51" net name from "" to "SPI0_MISO".

Changing component "U3:/56F352C0" pin "52" net name from "" to "SPI0_MOSI".

Changing component "U3:/56F352C0" pin "53" net name from "" to "Vbus_MOS_CTRL".

Changing component "U3:/56F352C0" pin "54" net name from "" to "5V_MOS_CTRL".

Changing component "U3:/56F352C0" pin "55" net name from "" to "3.3V_MOS_CTRL".

Changing component "U3:/56F352C0" pin "56" net name from "" to "LED_Status_2".

Changing component "U3:/56F352C0" pin "57" net name from "" to "LED_Status_1".

Changing component "U3:/56F352C0" pin "58" net name from "" to "LED_Heartbeat".

Changing component "U3:/56F352C0" pin "59" net name from "" to "UART2_RX".

Changing component "U3:/56F352C0" pin "60" net name from "" to "UART2_TX".

Changing component "U3:/56F352C0" pin "61" net name from "" to "Net-(U3-Pad61)".

Changing component "U3:/56F352C0" pin "62" net name from "" to "Net-(U3-Pad62)".

Changing component "U3:/56F352C0" pin "63" net name from "" to "Net-(U3-Pad63)".

Changing component "U3:/56F352C0" pin "64" net name from "" to "Net-(U3-Pad64)".

Info: Checking netlist component footprint "U4:/56DE92A4:SPEX_Parts:TSOP-6".

Adding new component "U4:/56DE92A4" footprint "SPEX_Parts:TSOP-6".

Changing component "U4:/56DE92A4" pin "6" net name from "" to "I2C1_SCL".

Changing component "U4:/56DE92A4" pin "1" net name from "" to "I2C1_SDA".

Changing component "U4:/56DE92A4" pin "5" net name from "" to "Net-(R12-Pad2)".

Changing component "U4:/56DE92A4" pin "2" net name from "" to "GND".

Changing component "U4:/56DE92A4" pin "4" net name from "" to "Net-(U4-Pad4)".

Changing component "U4:/56DE92A4" pin "3" net name from "" to "Net-(U4-Pad3)".

Info: Checking netlist component footprint "U5:/56DE9365:SPEX_Parts:TSOP-6".

Adding new component "U5:/56DE9365" footprint "SPEX_Parts:TSOP-6".

Changing component "U5:/56DE9365" pin "6" net name from "" to "I2C0_SCL".

Changing component "U5:/56DE9365" pin "1" net name from "" to "I2C0_SDA".

Changing component "U5:/56DE9365" pin "5" net name from "" to "Net-(R13-Pad2)".

Changing component "U5:/56DE9365" pin "2" net name from "" to "GND".

Changing component "U5:/56DE9365" pin "4" net name from "" to "Net-(U5-Pad4)".

Changing component "U5:/56DE9365" pin "3" net name from "" to "Net-(U5-Pad3)".

Info: Checking netlist component footprint "U6:/56EA9D25:SPEX_Parts:TSOP-6".

Adding new component "U6:/56EA9D25" footprint "SPEX_Parts:TSOP-6".

Changing component "U6:/56EA9D25" pin "6" net name from "" to "SPI0_MOSI".

Changing component "U6:/56EA9D25" pin "1" net name from "" to "SPI0_CS".

Changing component "U6:/56EA9D25" pin "5" net name from "" to "GND".

Changing component "U6:/56EA9D25" pin "2" net name from "" to "GND".

Changing component "U6:/56EA9D25" pin "4" net name from "" to "SPI0_MISO".

Changing component "U6:/56EA9D25" pin "3" net name from "" to "SPI0_SCK".

Info: Checking netlist component footprint "U7:/56DF35A9/56DF38C7:Housings_SSOP:MSOP-8_3x3mm_Pitch0.65mm".

Adding new component "U7:/56DF35A9/56DF38C7" footprint "Housings_SSOP:MSOP-8_3x3mm_Pitch0.65mm".

Changing component "U7:/56DF35A9/56DF38C7" pin "1" net name from "" to "I2C0_SDA".

Changing component "U7:/56DF35A9/56DF38C7" pin "2" net name from "" to "I2C0_SCL".

Changing component "U7:/56DF35A9/56DF38C7" pin "3" net name from "" to "/HAB Sensors/TempAlert".

Changing component "U7:/56DF35A9/56DF38C7" pin "4" net name from "" to "GND".

Changing component "U7:/56DF35A9/56DF38C7" pin "5" net name from "" to "+3V3".

Changing component "U7:/56DF35A9/56DF38C7" pin "6" net name from "" to "+3V3".

Changing component "U7:/56DF35A9/56DF38C7" pin "7" net name from "" to "+3V3".

Changing component "U7:/56DF35A9/56DF38C7" pin "8" net name from "" to "+3V3".

Info: Checking netlist component footprint "U8:/56DF35A9/56DF3C44:SPEX_Parts:LGA-8".

Adding new component "U8:/56DF35A9/56DF3C44" footprint "SPEX_Parts:LGA-8".

Changing component "U8:/56DF35A9/56DF3C44" pin "8" net name from "" to "+3V3".

Changing component "U8:/56DF35A9/56DF3C44" pin "1" net name from "" to "GND".

Changing component "U8:/56DF35A9/56DF3C44" pin "7" net name from "" to "GND".

Changing component "U8:/56DF35A9/56DF3C44" pin "2" net name from "" to "+3V3".

Changing component "U8:/56DF35A9/56DF3C44" pin "6" net name from "" to "+3V3".

Changing component "U8:/56DF35A9/56DF3C44" pin "3" net name from "" to "I2C0_SDA".

Changing component "U8:/56DF35A9/56DF3C44" pin "5" net name from "" to "GND".

Changing component "U8:/56DF35A9/56DF3C44" pin "4" net name from "" to "I2C0_SCL".

Info: Checking netlist component footprint "U9:/56DF35A9/56DF365D:SPEX_Parts:LGA-24".

Adding new component "U9:/56DF35A9/56DF365D" footprint "SPEX_Parts:LGA-24".

Changing component "U9:/56DF35A9/56DF365D" pin "1" net name from "" to "+3V3".

Changing component "U9:/56DF35A9/56DF365D" pin "2" net name from "" to "I2C0_SCL".

Changing component "U9:/56DF35A9/56DF365D" pin "3" net name from "" to "+3V3".

Changing component "U9:/56DF35A9/56DF365D" pin "4" net name from "" to "I2C0_SDA".

Changing component "U9:/56DF35A9/56DF365D" pin "5" net name from "" to "GND".

Changing component "U9:/56DF35A9/56DF365D" pin "6" net name from "" to "GND".

Changing component "U9:/56DF35A9/56DF365D" pin "7" net name from "" to "+3V3".

Changing component "U9:/56DF35A9/56DF365D" pin "8" net name from "" to "+3V3".

Changing component "U9:/56DF35A9/56DF365D" pin "9" net name from "" to "Net-(U9-Pad9)".

Changing component "U9:/56DF35A9/56DF365D" pin "10" net name from "" to "Net-(U9-Pad10)".

Changing component "U9:/56DF35A9/56DF365D" pin "11" net name from "" to "Net-(U9-Pad11)".

Changing component "U9:/56DF35A9/56DF365D" pin "12" net name from "" to "Net-(U9-Pad12)".

Changing component "U9:/56DF35A9/56DF365D" pin "13" net name from "" to "Net-(U9-Pad13)".

Changing component "U9:/56DF35A9/56DF365D" pin "14" net name from "" to "GND".

Changing component "U9:/56DF35A9/56DF365D" pin "15" net name from "" to "GND".

Changing component "U9:/56DF35A9/56DF365D" pin "16" net name from "" to "GND".

Changing component "U9:/56DF35A9/56DF365D" pin "17" net name from "" to "GND".

Changing component "U9:/56DF35A9/56DF365D" pin "18" net name from "" to "GND".

Changing component "U9:/56DF35A9/56DF365D" pin "19" net name from "" to "GND".

Changing component "U9:/56DF35A9/56DF365D" pin "20" net name from "" to "GND".

Changing component "U9:/56DF35A9/56DF365D" pin "21" net name from "" to "Net-(C12-Pad1)".

Changing component "U9:/56DF35A9/56DF365D" pin "22" net name from "" to "+3V3".

Changing component "U9:/56DF35A9/56DF365D" pin "23" net name from "" to "+3V3".

Changing component "U9:/56DF35A9/56DF365D" pin "24" net name from "" to "Net-(C13-Pad1)".

Info: Checking netlist component footprint "U10:/56DF35A9/56E7BAB9:TO_SOT_Packages_SMD:SOT-23-5".

Adding new component "U10:/56DF35A9/56E7BAB9" footprint "TO_SOT_Packages_SMD:SOT-23-5".

Changing component "U10:/56DF35A9/56E7BAB9" pin "1" net name from "" to "Net-(U10-Pad1)".

Changing component "U10:/56DF35A9/56E7BAB9" pin "2" net name from "" to "GND".

Changing component "U10:/56DF35A9/56E7BAB9" pin "3" net name from "" to "Net-(U10-Pad3)".

Changing component "U10:/56DF35A9/56E7BAB9" pin "4" net name from "" to "/HAB Sensors/2.5VRefVoltage".

Changing component "U10:/56DF35A9/56E7BAB9" pin "5" net name from "" to "GND".

Info: Checking netlist component footprint "U11:/56EB0DA0/56EBFBDF:Power_Integrations:SO-8".

Adding new component "U11:/56EB0DA0/56EBFBDF" footprint "Power_Integrations:SO-8".

Changing component "U11:/56EB0DA0/56EBFBDF" pin "1" net name from "" to "CAN0_TX".

Changing component "U11:/56EB0DA0/56EBFBDF" pin "2" net name from "" to "GND".

Changing component "U11:/56EB0DA0/56EBFBDF" pin "3" net name from "" to "+3V3".

Changing component "U11:/56EB0DA0/56EBFBDF" pin "4" net name from "" to "CAN0_RX".

Changing component "U11:/56EB0DA0/56EBFBDF" pin "5" net name from "" to "Net-(U11-Pad5)".

Changing component "U11:/56EB0DA0/56EBFBDF" pin "6" net name from "" to "/Data_Input_Output/CANL_out".

Changing component "U11:/56EB0DA0/56EBFBDF" pin "7" net name from "" to "/Data_Input_Output/CANH_out".

Changing component "U11:/56EB0DA0/56EBFBDF" pin "8" net name from "" to "Net-(R28-Pad1)".

Info: Checking netlist component footprint "U12:/56EB0DA0/56EB2066:Power_Integrations:SO-8".

Adding new component "U12:/56EB0DA0/56EB2066" footprint "Power_Integrations:SO-8".

Changing component "U12:/56EB0DA0/56EB2066" pin "1" net name from "" to "UART0_RX".

Changing component "U12:/56EB0DA0/56EB2066" pin "2" net name from "" to "RX/TX_CTRL".

Changing component "U12:/56EB0DA0/56EB2066" pin "3" net name from "" to "RX/TX_CTRL".

Changing component "U12:/56EB0DA0/56EB2066" pin "4" net name from "" to "UART0_TX".

Changing component "U12:/56EB0DA0/56EB2066" pin "5" net name from "" to "GND".

Changing component "U12:/56EB0DA0/56EB2066" pin "6" net name from "" to "/Data_Input_Output/RS485_A".

Changing component "U12:/56EB0DA0/56EB2066" pin "7" net name from "" to "/Data_Input_Output/RS485_B".

Changing component "U12:/56EB0DA0/56EB2066" pin "8" net name from "" to "+3V3".

Info: Checking netlist component footprint "U13:/56EB0DA0/56EB178F:SPEX_Parts:SCHA4B0400".

Adding new component "U13:/56EB0DA0/56EB178F" footprint "SPEX_Parts:SCHA4B0400".

Info: Checking netlist component footprint "U14:/56FB6452:SMD_Packages:SOIC-8-N".

Adding new component "U14:/56FB6452" footprint "SMD_Packages:SOIC-8-N".

Changing component "U14:/56FB6452" pin "8" net name from "" to "SPI0_MISO".

Changing component "U14:/56FB6452" pin "7" net name from "" to "GND".

Changing component "U14:/56FB6452" pin "6" net name from "" to "+3V3".

Changing component "U14:/56FB6452" pin "5" net name from "" to "Net-(U14-Pad5)".

Changing component "U14:/56FB6452" pin "4" net name from "" to "SPI0_CS1".

Changing component "U14:/56FB6452" pin "3" net name from "" to "Net-(U14-Pad3)".

Changing component "U14:/56FB6452" pin "2" net name from "" to "SPI0_SCK".

Changing component "U14:/56FB6452" pin "1" net name from "" to "SPI0_MOSI".

Info: Checking netlist component footprint "Y1:/5679D91C:SPEX_Parts:CX3225GB16000D0HPQCC".

Adding new component "Y1:/5679D91C" footprint "SPEX_Parts:CX3225GB16000D0HPQCC".

Changing component "Y1:/5679D91C" pin "1" net name from "" to "Net-(C7-Pad1)".

Changing component "Y1:/5679D91C" pin "2" net name from "" to "Net-(C8-Pad1)".

Error: Component 'K1' pad '1' not found in footprint 'SPEX_Parts:G5LE-1A4-DC3'

Error: Component 'K2' pad '1' not found in footprint 'SPEX_Parts:G5LE-1A4-DC3'

Error: Component 'U13' pad '7' not found in footprint 'SPEX_Parts:SCHA4B0400'

Error: Component 'U13' pad '3' not found in footprint 'SPEX_Parts:SCHA4B0400'

Error: Component 'U13' pad '5' not found in footprint 'SPEX_Parts:SCHA4B0400'

Error: Component 'U13' pad '2' not found in footprint 'SPEX_Parts:SCHA4B0400'

Error: Component 'U13' pad '9' not found in footprint 'SPEX_Parts:SCHA4B0400'

Error: Component 'U13' pad '6' not found in footprint 'SPEX_Parts:SCHA4B0400'

Error: Component 'U13' pad '10' not found in footprint 'SPEX_Parts:SCHA4B0400'

Error: Component 'U13' pad '4' not found in footprint 'SPEX_Parts:SCHA4B0400'

Error: Component 'U13' pad '8' not found in footprint 'SPEX_Parts:SCHA4B0400'

Error: Component 'U13' pad '1' not found in footprint 'SPEX_Parts:SCHA4B0400'

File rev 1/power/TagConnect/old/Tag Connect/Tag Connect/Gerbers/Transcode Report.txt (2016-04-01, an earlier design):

   ---- Transcoding 'C:\Users\neil\Documents\Tag-Connect\Footprint Decals\To Check\KiCad\Tag Connect\Tag Connect\Gerbers\Tag-Front.gtl' ----   Fri Sep 28 00:41:12 2012

D11   --> D100
-----------------------------------------------------------------

   ---- Transcoding 'C:\Users\neil\Documents\Tag-Connect\Footprint Decals\To Check\KiCad\Tag Connect\Tag Connect\Gerbers\Tag-Mask_Back.gbs' ----   Fri Sep 28 00:41:12 2012

D11   --> D101
D12   --> D102
-----------------------------------------------------------------

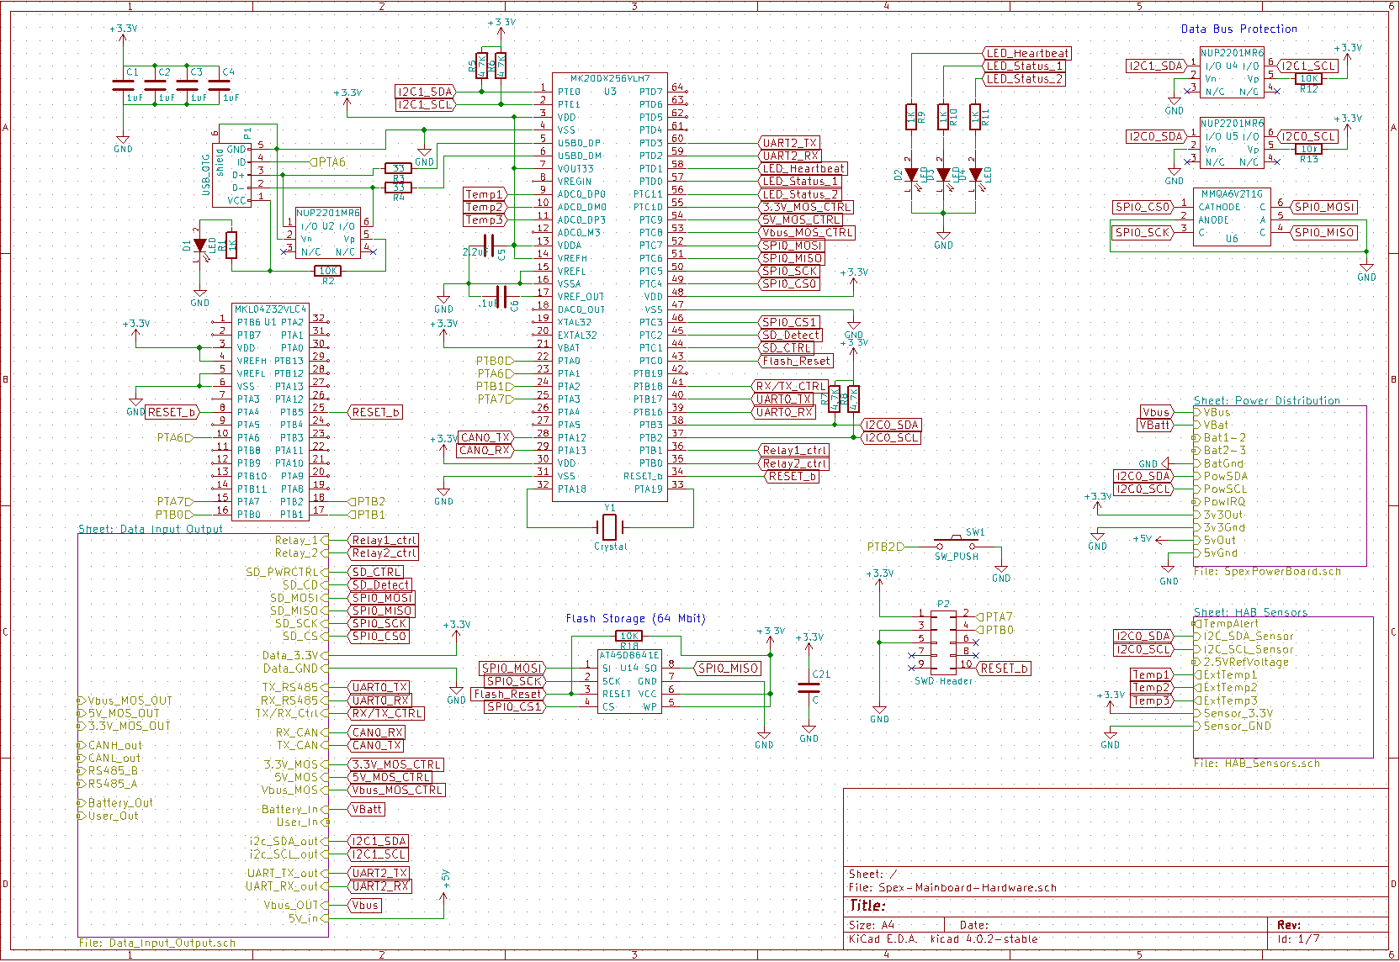
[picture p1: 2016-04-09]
rev 1/images/Spex-Mainboard-Hardware_4_8_16.png

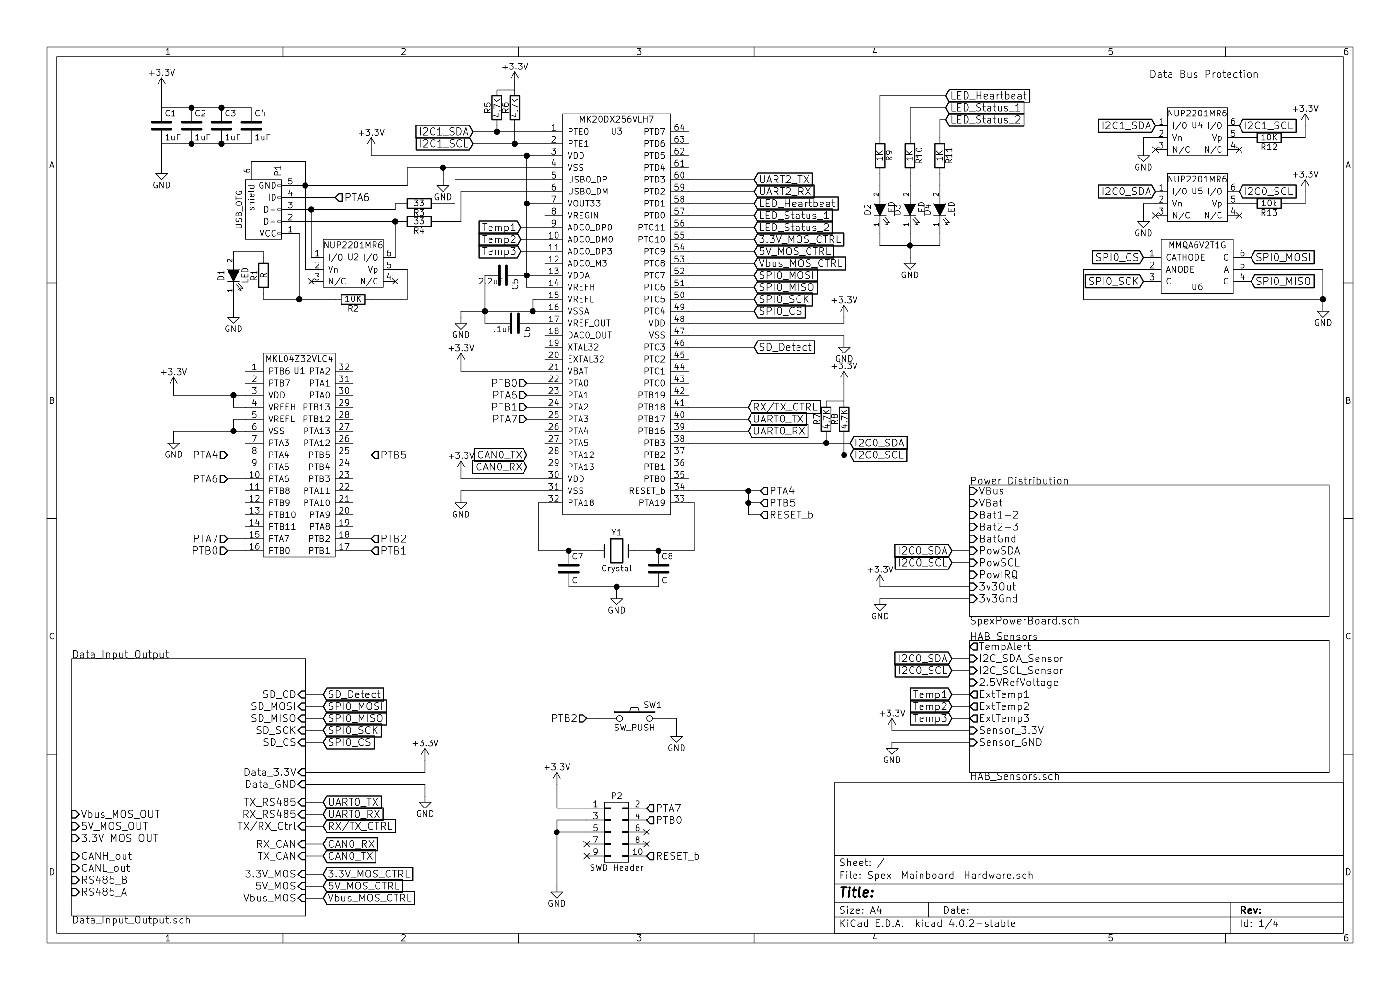
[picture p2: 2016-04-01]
Spex-Mainboard-Hardware.png

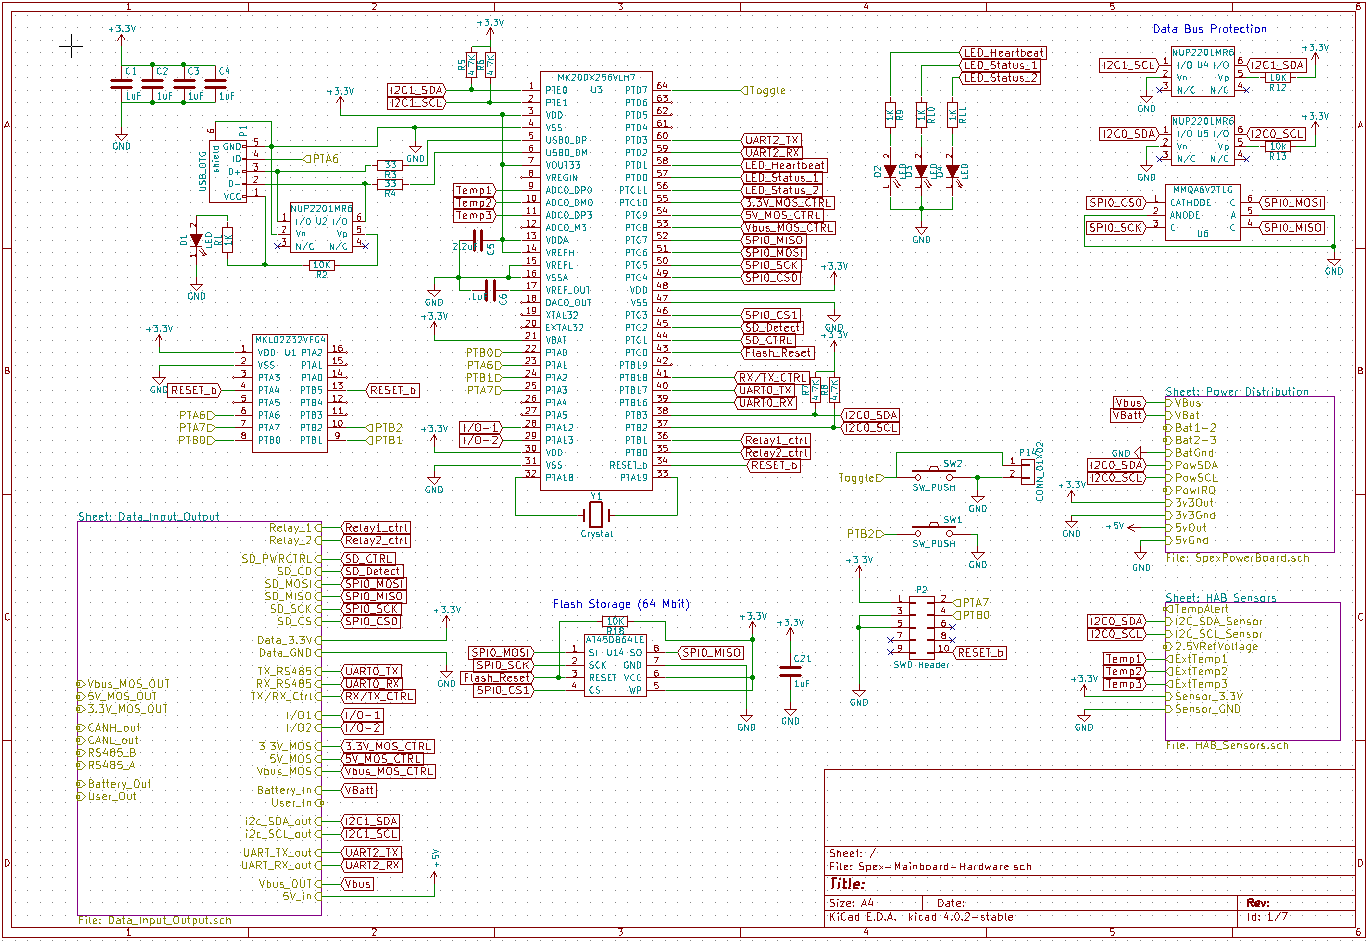
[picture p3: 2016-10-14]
images/Spex-Mainboard-Hardware_10_13_16.png

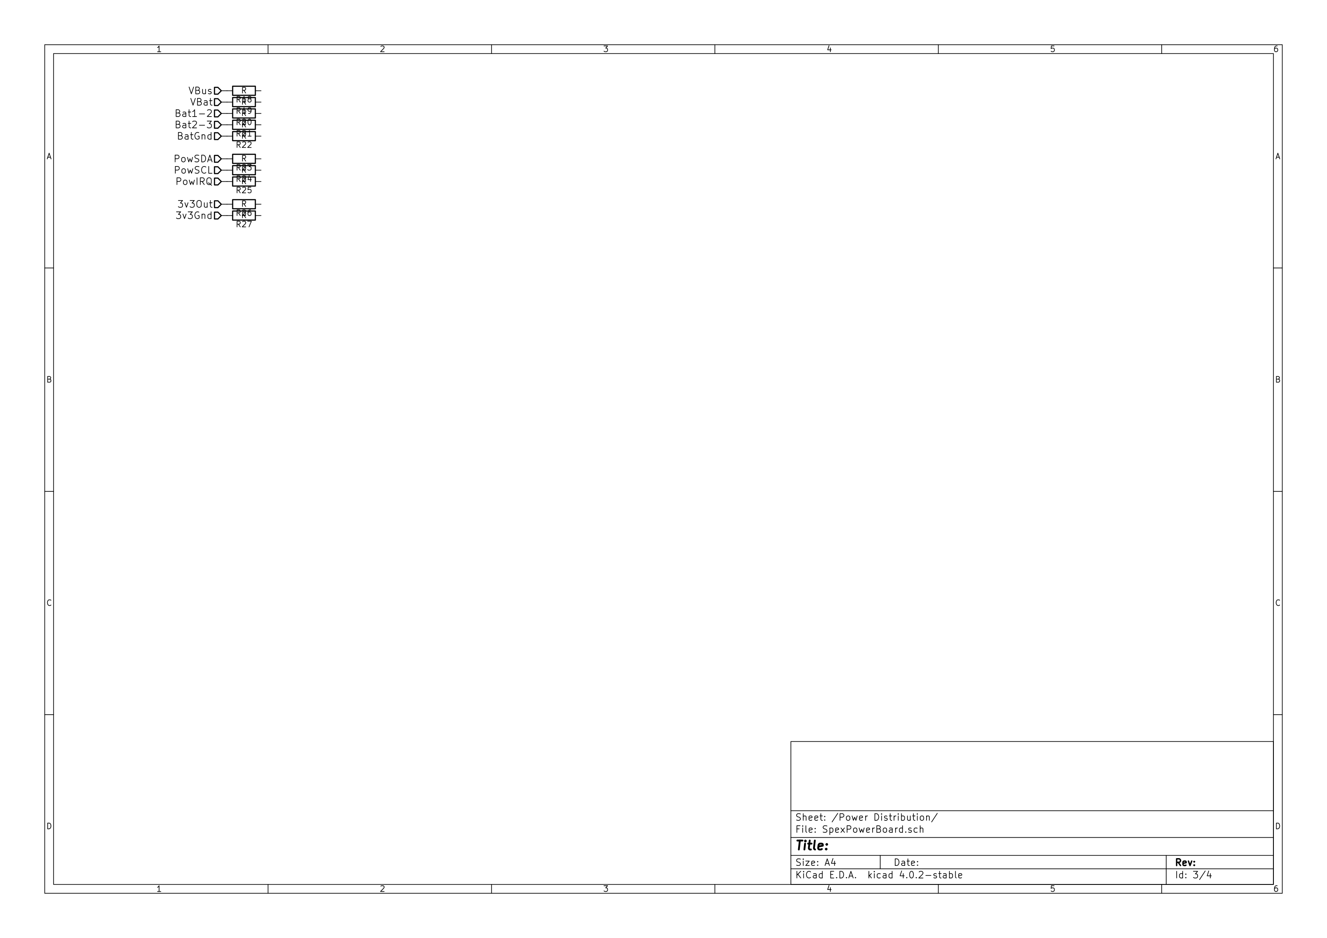
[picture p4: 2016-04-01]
SpexPowerBoard-Power Distribution.png

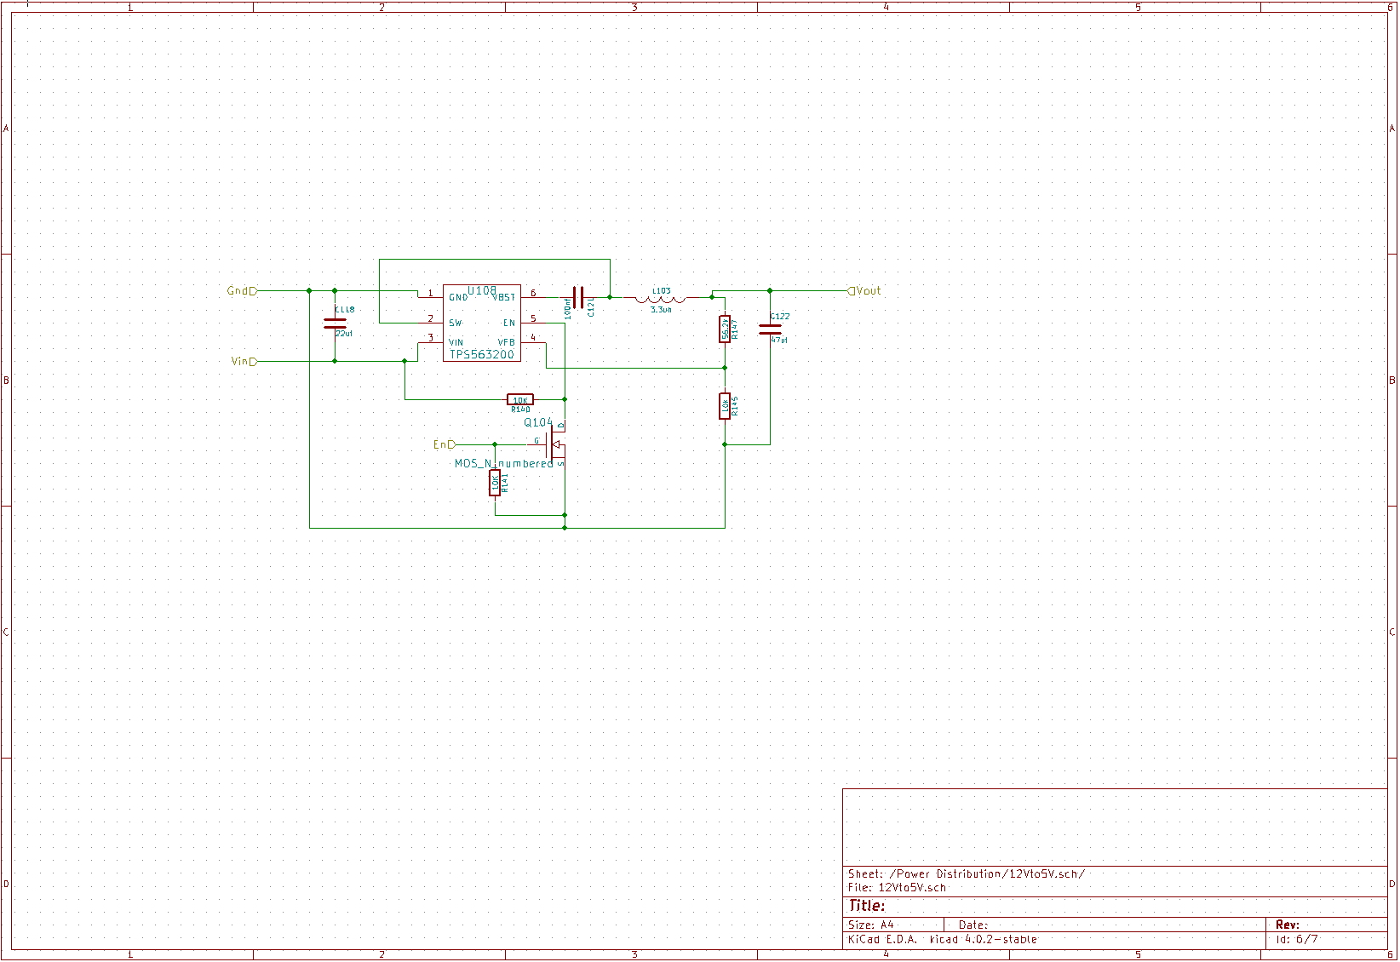
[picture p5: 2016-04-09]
rev 1/images/Power_Distribuition_5VRegulator.PNG

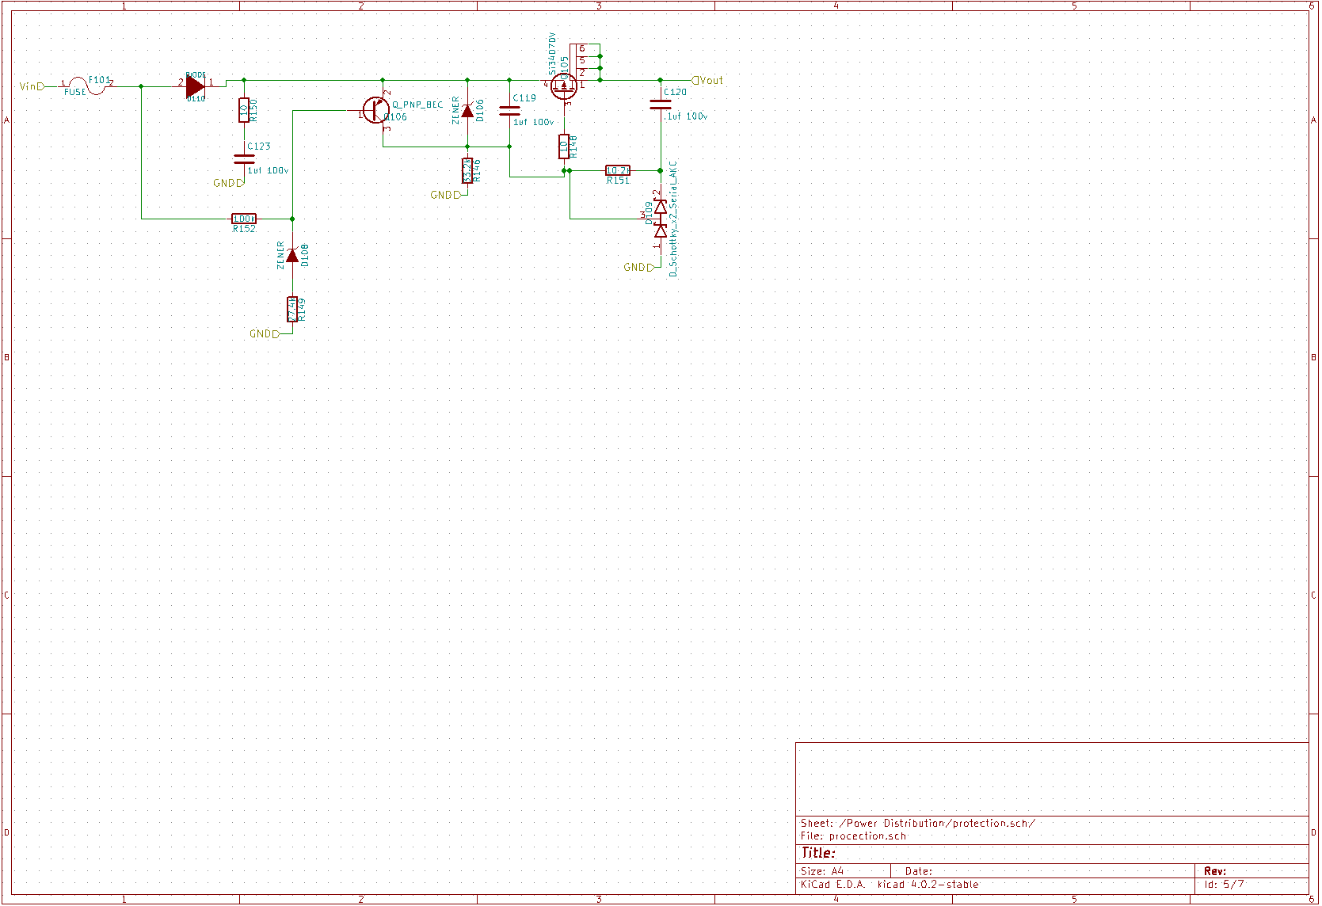
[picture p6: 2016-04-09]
rev 1/images/Power_Distribuition_Protection.PNG

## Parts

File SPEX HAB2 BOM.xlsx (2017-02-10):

Bill of Materials (BOM) - RIT High Altitude Balloon Test 1 (HAB1)
> All parts seperated by color, GREEN for Mainboard, BLUE for Balloon board.
Item # | Qty | Ref Des | Manufacturer | Mfg Part # | Dist. Part # | Price Per Unit | Total Price | Description | Package | Type | Datasheet | Notes
1 | 1 | U1 | PJRC | MKL02z32VFG4 |  | $6.80 | $6.80 | Secondary Microcontroller/Bootloader | QFN-16 | SMD | http://www.pjrc.com/store/ic_mkl02.html
2 | 3 | U2,U4,U5 | ON Semicondutor | NUP2201MR6T1G | 863-NUP2201MR6T1G | $0.55 | $1.65 | ESD Protection 2 lines | TSOP-6 | SMD
3 | 1 | U3 | NXP / Freescale | MK20DX256VLH7 | 841-MK20DX256VLH7 | $7.07 | $7.07 | Primary Microcontroller | LQFP-64 | SMD
4 | 1 | U6 | ON Semicondutor | MMQA6V2T1G | 863-MMQA6V2T1G | $0.48 | $0.48 | ESD Protection 4 lines | TSOP-6 | SMD
5 | 1 | U7 | Microchip Technology | MCP9808T-E/MS | 579-MCP9808T-E/MS | $1.22 | $1.22 | Temperature Sensor | MSOP-8 | SMD
6 | 1 | U8 | Bosch Sensortec | BME280 | 262-BME280 | $5.66 | $5.66 | Altimeter (pressure temperature) | LGA-8 | SMD
7 | 1 | U9 | STMicroelectronics | LSM9DS1TR | 511-LSM9DS1TR | $6.21 | $6.21 | 9DOF IMU (accel, gyro, compass) | LGA-24 | SMD
8 | 1 | U10 | Texas Instruments | LM4030BMF-2.5/NOPB | 926-LM4030BMF25NOPB | $2.12 | $2.12 | 2.5V precision voltage reference | SOT23-6 | SMD
10 | 1 | U12 | STMicroelectronics | ST1480ABDR | 511-ST1480ABDR | $1.40 | $1.40 | RS485 Transceiver | SO-8 | SMD
11 | 1 | U13 | ALPS | SCHA4B0419 | 688-SCHA4B0419 | $0.80 | $0.80 | MicroSD card slot |  | SMD
12 | 2 | U105,U108 | Texas Instruments | TPS563200DDCR | 595-TPS563200DDCR | $1.45 | $2.90 | 3.3V/5V Power Regulator | SOT-23-6 | SMD
13 | 1 | Y1 | AVX | CX3225GB16000D0HPQCC | 581-CX3225GB16DHPQCC | $0.72 | $0.72 | 16mhz cyrstal |  | SMD
14 | 1 | SW1 | CTS Electronic Components | 222AMVBAR | 774-222AMVBAR | $0.42 | $0.42 | reset button | Gull Wing | SMD
15 | 1 | SW2 |  |  |  | $0.00 | $0.00 |  |  | SMD
16 | 3 | TH1,TH2,TH3 | Vishay / BC Components | NTCLE100E3103JB0 | 594-2381-640-63103 | $0.26 | $0.78 | Thermistor | BULK | Thru Hole
17 | 1 | Q3 | Infineon Technologies | BSS215P H6327 | 726-BSS215PH6327XT | $0.46 | $0.46 | P channel mosfet |  | SMD
18 | 3 | Q4,Q5,Q6 | Vishay Semiconductors | Si5468DC-T1-GE3 | 781-SI5468DC-GE3 | $0.52 | $1.56 | N channel power mosfet |  | SMD
19 | 1 | Q105 | Vishay Semiconductors | SI3407DV-T1-GE3 | 781-SI3407DV-GE3 | $0.52 | $0.52 | N channel power mosfet |  | SMD
20 | 1 | Q106 | ON Semicondutor | MMBT3906LT1G | 863-MMBT3906LT1G | $0.10 | $0.10 | BJT Transistor | SOT-23 | SMD | http://www.mouser.com/ds/2/308/MMBT3906LT1-D-112192.pdf
21 | 1 | D1 | Kingbright | AP1608SGC | 604-AP1608SGC | $0.13 | $0.13 | Green LED | 0603 | SMD | http://www.mouser.com/ds/2/216/AP1608SGC-29521.pdf
22 | 1 | D2 | OSRAM Opto | LB Q39G-L2OO-35-1 | 720-LBQ39GL2N2351 | $0.15 | $0.15 | Blue LED | 0603 | SMD
23 | 1 | D3,D4 | OSRAM Opto | LS Q976-NR-1 | 720-LSQ976-NR-1 | $0.10 | $0.10 | Red LED | 0603 | SMD | http://www.mouser.com/ds/2/311/LS%20Q976%20-%20CHIPLED%200603-741036.pdf
24 | 2 | D106,D108 | Diodes Incorportated | BZT52C16-7-F | 621-BZT52C16-F | $0.19 | $0.38 |  |  | SMD
25 | 1 | D109 | ON Semicondutor | BAV99WT1G | 863-BAV99WT1G | $0.00 | $0.00 |  |  | SMD
26 | 1 | L102 | Laird Technologies | TYS50402R2N-10 | 875-TYS50402R2N-10 | $0.38 | $0.38 | 2.2uH Inductor |  | SMD
27 | 1 | L103 | Taiyo Yuden | NRS8030T3R3MJGJ | 963-NRS8030T3R3MJGJ | $0.48 | $0.48 | 3.3uH Inductor | 8030 | SMD
28 | 1 | D110 | Diodes Incorportated | B340-13-F | 621-B340-F | $0.34 | $0.34 | input diode |  | SMD
29 | 1 | F101 | Bourns | MF-LSMF260X-2 | 652-MF-LSMF260X-2 | $0.46 | $0.46 | Resetable fuse | 3121 | SMD
30 | 1 | P1 | JAE Electronics | DX4R005JJ6R1500 | 656-DX4R005JJ6R1500 | $0.97 | $0.97 | MicroB USB connector |  | Thru Hole
31 | 4 | P3,P4,P5,P6 | JST (Sparkfun) |  | PRT-09916 | $1.50 | $6.00 | JST PH 4 pin (full assembly) | CONN | Thru Hole | https://www.sparkfun.com/products/9916
32 | 7 | P7,P8,P9,P10,P11,P12,P13 | Molex | 172310-1102 | 538-172310-1102 | $0.72 | $5.04 | UltraFit 2pin Header(male) | CONN | Thru Hole
33 | 4 | R1,R9,R10,R11 | Panasonic | ERJ-3EKF1001V | 667-ERJ-3EKF1001V | $0.10 | $0.40 | 1k ohm resistor | 0603 | SMD | http://www.mouser.com/ds/2/315/AOA0000CE2-37512.pdf | order 100
34 | 14 | R2,R12,R13,R20,R30,R31,R35,R36,R37,R38,R109,R126,R130,R140,R145 | Panasonic | ERJ-3GEYJ103V | 667-ERJ-3GEYJ103V | $0.10 | $1.40 | 10k ohm resistor | 0603 | SMD |  | order 100
35 | 2 | R21,R22 | KOA Speer | RK73B1JTTDD513J | 660-RK73B1JTTDD513J | $0.08 | $0.16 | 51k ohm resistor | 0603 | SMD | http://www.mouser.com/ds/2/219/RK73B-919.pdf
36 | 2 | R3,R4 | Vishay / Dale | CRCW060333R0FKEA | 71-CRCW0603-33-E3 | $0.10 | $0.20 | 33 ohm resistor | 0603 | SMD
37 | 3 | R14,R15,R16 | Susumu | RR0816P-123-D | 754-RR0816P-123D | $0.10 | $0.30 | 12k ohm resistor (0.5%) | 0603 | SMD | http://www.mouser.com/ds/2/392/susumu_RR_Data_Sheet-358748.pdf
38 | 1 | R17 | KOA Speer | RK73B1JTTDD241J | 660-RK73B1JTTDD241J | $0.08 | $0.08 | 240 ohm resistor | 0603 | SMD | http://www.mouser.com/ds/2/219/RK73B-919.pdf
39 | 5 | R5,R6,R7,R8,R28 | Panasonic | ERJ-3EKF4701V | 667-ERJ-3EKF4701V | $0.10 | $0.50 | 4.7k ohm resistor | 0603 | SMD | http://www.mouser.com/ds/2/315/AOA0000CE2-37512.pdf | order 100
40 | 1 | R33 | KOA Speer | RK73B1JTTDD121J | 660-RK73B1JTTDD121J | $0.08 | $0.08 | 120 ohm resistor | 0603 | SMD | http://www.mouser.com/ds/2/219/RK73B-919.pdf
41 | 2 | R108,R146 | Panasonic | ERJ-3EKF3322V | 667-ERJ-3EKF3322V | $0.10 | $0.20 | 33.2k ohm resistor | 0603 | SMD | http://www.mouser.com/ds/2/427/dcrcwe3-109170.pdf
42 | 1 | R147 | Panasonic | ERJ-3EKF5622V | 667-ERJ-3EKF5622V | $0.10 | $0.10 | 56.2k ohm resistor | 0603 | SMD | http://www.mouser.com/ds/2/315/AOA0000CE2-37512.pdf
43 | 2 | R148, R150 | Panasonic | ERJ-3EKF10R0V | 667-ERJ-3EKF10R0V | $0.10 | $0.20 | 10 ohm resistor | 0603 | SMD | http://www.mouser.com/ds/2/315/AOA0000CE2-37512.pdf
44 | 1 | R149 | Bourns | CR0603-FX-2742ELF | 652-CR0603FX-2742ELF | $0.10 | $0.10 | 27.4K ohm resistor | 0603 | SMD | http://www.mouser.com/ds/2/54/hpreztr-777398.pdf
45 | 1 | R151 | Panasonic | ERJ-3EKF1022V | 667-ERJ-3EKF1022V | $0.10 | $0.10 | 10.2k ohm resistor | 0603 | SMD | http://www.mouser.com/ds/2/315/AOA0000CE2-37512.pdf
46 | 1 | R152 | Vishay | RCA0603100KJNEC | 71-RCA0603100KJNEC | $0.09 | $0.09 | 100k ohm resistor | 0603 | SMD | http://www.mouser.com/ds/2/427/rcae3-515375.pdf
47 | 8 | C1,C2,C3,C4,C18,C21,C2 | Wurth Electronics | 885012106017 | 710-885012106017 | $0.08 | $0.64 | 1uF capacitor | 0603 | SMD
48 | 1 | C5 | Yageo | CC0603MRX5R5BB225 | 603-CC603MRX5R5BB225 | $0.10 | $0.10 | 2.2uF capacitor | 0603 | SMD | http://www.mouser.com/ds/2/447/UPY-GPHC_X5R_4V-to-50V_14_0717-202131.pdf
49 | 8 | C6,C9,C10,C11,C13,C15,C19,C121 | Wurth Electronics | 885012206071 | 710-885012206071 | $0.04 | $0.32 | 100nF capacitor (0.1uf) | 0603 | SMD
50 | 1 | C109 | Wurth Electronics | 885012105016 | 710-885012105016 | $0.02 | $0.02 | 100nF capacitor | 0402 | SMD | http://www.mouser.com/ds/2/445/885012105016-611018.pdf
51 | 1 | C12 | Wurth Electronics | 885012206040 | 710-885012206040 | $0.04 | $0.04 | 10nF capacitor (0.01uf) | 0603 | SMD | http://www.mouser.com/ds/2/445/885012206040-555095.pdf
52 | 1 | C14 | Yageo | CC0603KRX5R5BB475 | 603-CC603KRX5R5BB475 | $0.11 | $0.11 | 4.7uF capacitor | 0603 | SMD
53 | 2 | C16,C20 | Murata Electronics | GRM188R61A106KE69D | 81-GRM188R61A106KE9D | $0.20 | $0.40 | 10uF capacitor | 0603 | SMD | http://www.murata.com/products/catalog/pdf/c02e.pdf
54 | 2 | C105,C122 | Yageo | CC1206MKX5R5BB476 | 603-CC126MKX5R5BB476 | $0.50 | $1.00 | 47uF capacitor | 1206 | SMD
55 | 2 | C114,C118 | Murata Electronics | GRM31CR61E226ME15L | 81-GRM31CR61E226ME5L | $0.50 | $1.00 | 22uF capacitor | 1206 | SMD | http://www.murata.com/products/catalog/pdf/c02e.pdf
56 | 2 | C119, C123 | Taiyo Yuden | HMK316B7105KL-T | 963-HMK316B7105KL-T | $0.43 | $0.86 | 1uF capacitor (100V) | 1206 | SMD
57 | 1 | C120 | Vishay / Vitramon | VJ1206Y104JXBTW1BC | 77-VJ1206Y104JXBTBC | $0.10 | $0.10 | 0.1uF capacitor (100V) | 1206 | SMD | http://www.mouser.com/ds/2/427/vjw1bcbascomseries-223529.pdf
58 | 7 |  | Molex | 172256-1102 | 538-172256-1102 | $0.31 | $2.17 | UltraFit 2pin (female) |  |  | http://www.mouser.com/ds/2/276/1722561102_CRIMP_HOUSINGS-705529.pdf
59 | 14 |  | Molex | 1722533123 | WM11561CT-ND | $0.15 | $2.13 | ultrafit contacts (20awg wire) |  |  | http://www.mouser.com/ds/2/276/1722533023_sd-587746.pdf | DIGIKEY
1 | 1 | U1 | STMicroelectronics | ST1480ABDR | 511-ST1480ABDR | $1.40 | $1.40 | RS485 Transceiver | SO-8 | SMD
2 | 1 | U2 | ON Semiconductor | NCP500SN33T1G | 863-NCP500SN33T1G | $0.64 | $0.64 | 3.3V Linear Power Regulator | TSOP-5 | SMD
3 | 1 | U3 | NXP / Freescale | MKL03Z32VFG4 | 841-MKL03Z32VFG4 | $1.24 | $1.24 | Microcontroller | QFN-16 | SMD
4 | 1 | U4 | Bosch Sensortec | BME280 | 262-BME280 | $5.66 | $5.66 | Altimeter (pressure temperature) | LGA-8 | SMD
5 | 1 | U7 | Linear Technology | LT6105IDCB#TRMPBF | LT6105IDCB#TRMPBFCT-ND | $2.84 | $2.84 | Current Sense Op Amp | 6-WFDFN | SMD |  | DIGIKEY
6 | 1 | Q1 | International Rectifier | IRLL3303PbF | 942-IRLL3303PBF | $0.86 | $0.86 | Niachrome trigger mosfet | SOT-223-4 | SMD
7 | 1 | D1 | OSRAM Opto | LB Q39G-L2OO-35-1 | 720-LBQ39GL2N2351 | $0.15 | $0.15 | Blue LED | 0603 | SMD
8 | 1 | P1 | Molex | PicoBlade_53047-0610 | 538-53047-0610 | $0.67 | $0.67 | Picoblade 6 pin | CONN | Thru Hole
9 | 1 | R1 | Panasonic | ERJ-2GEJ202X | 667-ERJ-2GEJ202X | $0.10 | $0.10 | 2k ohm resistor | 0402 | SMD
10 | 1 | R2 | Vishay / Dale | CRCW04020000Z0ED | 71-CRCW0402-0-E3 | $0.10 | $0.10 | 0 ohm resistor | 0402 | SMD
11 | 3 | R3,R16,R18 | KOA Speer | RK73B1ETTP101J | 660-RK73B1ETTP101J | $0.10 | $0.30 | 100 ohm resistor | 0402 | SMD | http://www.mouser.com/ds/2/219/RK73B-919.pdf
12 | 2 | R6,R7 | Panasonic | ERJ-2RKF4701X | 667-ERJ-2RKF4701X | $0.10 | $0.20 | 4.7k ohm resistor | 0402 | SMD | http://www.mouser.com/ds/2/315/AOA0000CE2-37512.pdf
13 | 1 | R8 | KOA Speer | RK73H1ETTP1200F | 660-RK73H1ETTP1200F | $0.10 | $0.10 | 120 ohm resistor | 0402 | SMD | http://www.mouser.com/ds/2/219/RK73H-5715.pdf
14 | 1 | R19 | Welwyn Components | LRMAM0805-R02FT5 | 756-LRMAM0805R02FT5 | $0.37 | $0.37 | .02 ohm resistor | 0805 | SMD
15 | 1 | R20 | KOA Speer | RK73H1ETTP1001F | 660-RK73H1ETTP1001F | $0.10 | $0.10 | 1k ohm resistor | 0402 | SMD | http://www.mouser.com/ds/2/219/RK73H-5715.pdf
16 | 5 | C1,C2,C5,C7,C18 | Wurth Electronics | 885012105012 | 710-885012105012 | $0.05 | $0.25 | 1uF capacitor | 0402 | SMD | http://www.mouser.com/ds/2/445/885012105012-555006.pdf
17 | 1 | C3 | Yageo | CC0603MRX5R5BB225 | 603-CC603MRX5R5BB225 | $0.10 | $0.10 | 2.2uF capacitor | 0603 | SMD
18 | 1 | C4 | Yageo | CC0603KRX5R5BB475 | 603-CC603KRX5R5BB475 | $0.11 | $0.11 | 4.7uF capacitor | 0603 | SMD
19 | 6 |  | Molex | 500588000 | WM1775CT-ND | $0.10 | $0.60 | picoblade contacts |  |  |  | DIGIKEY
20 | 1 |  | Molex | 51021-0600 | 538-51021-0600 | $0.36 | $0.36
 |  |  |  |  | Board Multiplier: | 1 | Mainboard Total:
 |  |  |  |  |  |  | $68.10
 |  |  |  |  |  |  | Balloon Total:
 |  |  |  |  |  |  | $16.15
 |  |  |  |  |  |  | Grand Total:
 |  |  |  |  |  |  | $84.25

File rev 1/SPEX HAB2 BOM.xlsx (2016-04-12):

Bill of Materials (BOM) - RIT High Altitude Balloon Test 1 (HAB1)
> All parts seperated by color, GREEN for Mainboard, BLUE for Balloon board.
Item # | Qty | Ref Des | Manufacturer | Mfg Part # | Dist. Part # | Price Per Unit | Total Price | Description | Package | Type | Datasheet | Notes
1 | 2 | U1 | PJRC | MKL04Z32VLC4 |  | $6.00 | $12.00 | Secondary Microcontroller/Bootloader |  | SMD
2 | 6 | U2,U4,U5 | ON Semicondutor | NUP2201MR6T1G | 863-NUP2201MR6T1G | $0.55 | $3.30 | ESD Protection 2 lines |  | SMD
3 | 2 | U3 | NXP / Freescale | MK20DX256VLH7 | 841-MK20DX256VLH7 | $7.07 | $14.14 | Primary Microcontroller |  | SMD
4 | 2 | U6 | ON Semicondutor | MMQA6V2T1G | 863-MMQA6V2T1G | $0.48 | $0.96 | ESD Protection 4 lines |  | SMD
5 | 2 | U7 | Microchip Technology | MCP9808T-E/MS | 579-MCP9808T-E/MS | $1.22 | $2.44 | Temperature Sensor |  | SMD
6 | 2 | U8 | Bosch Sensortec | BME280 | 262-BME280 | $5.66 | $11.32 | Altimeter (pressure temperature) | LGA-8 | SMD
7 | 2 | U9 | STMicroelectronics | LSM9DS1TR | 511-LSM9DS1TR | $6.21 | $12.42 | 9DOF IMU (accel, gyro, compass) | LGA-24 | SMD
8 | 2 | U10 | Texas Instruments | LM4030BMF-2.5/NOPB | 926-LM4030BMF25NOPB | $2.12 | $4.24 | 2.5V precision voltage reference | SOT23-6 | SMD
9 | 2 | U11 | Microchip Technology | MCP2551-I/SN | 579-MCP2551-I/SN | $1.12 | $2.24 | CAN Transceiver |  | SMD
10 | 2 | U12 | STMicroelectronics | ST1480ABDR | 511-ST1480ABDR | $1.40 | $2.80 | RS485 Transceiver | SO-8 | SMD
11 | 2 | U13 | ALPS | SCHA4B0419 | 688-SCHA4B0419 | $0.80 | $1.60 | MicroSD card slot |  | SMD
12 | 2 | U14 | Adesto Technologies | AT45DB641E-SHN-B | 988-AT45DB641E-SHN-B | $4.00 | $8.00 | 64Mbit flash storage |  | SMD
13 | 4 | U105,U108 | Texas Instruments | TPS563200DDCR | 595-TPS563200DDCR | $1.45 | $5.80 | 3.3V/5V Power Regulator |  | SMD
14 | 2 | Y1 | AVX | CX3225GB16000D0HPQCC | 581-CX3225GB16DHPQCC | $0.72 | $1.44 | 16mhz cyrstal |  | SMD
15 | 2 | SW1 | CTS Electronic Components | 222AMVBAR | 774-222AMVBAR | $0.42 | $0.84 | reset button | Gull Wing | SMD
16 | 6 | TH1,TH2,TH3 | Vishay / BC Components | NTCLE100E3103JB0 | 594-2381-640-63103 | $0.26 | $1.56 | Thermistor | BULK | Thru Hole
17 | 4 | Q1,Q2 | ON Semicondutor | 2N7002KT1G | 863-2N7002KT1G | $0.20 | $0.80 | N channel mosfet |  | SMD
19 | 2 | Q3 | Infineon Technologies | BSS215P H6327 | 726-BSS215PH6327XT | $0.46 | $0.92 | P channel mosfet |  | SMD
20 | 6 | Q4,Q5,Q6 | Vishay Semiconductors | Si5468DC-T1-GE3 | 781-SI5468DC-GE3 | $0.52 | $3.12 | N channel power mosfet |  | SMD
21 | 4 | Q101,Q104 | Diodes Incorportated | DMG2302U-7 | 621-DMG2302U-7 | $0.37 | $1.48 | Enable pin Nchannel Mosfet | SOT23-3 | SMD
22 | 2 | Q105 | Vishay Semiconductors | SI3407DV-T1-GE3 | 781-SI3407DV-GE3 | $0.52 | $1.04 | N channel power mosfet |  | SMD
23 | 2 | Q106 | ON Semicondutor | MMBT3906LT1G | 863-MMBT3906LT1G | $0.10 | $0.20 | BJT Transistor | SOT-23 | SMD | http://www.mouser.com/ds/2/308/MMBT3906LT1-D-112192.pdf
24 | 2 | D1 | Kingbright | AP1608SGC | 604-AP1608SGC | $0.13 | $0.26 | Green LED | 0603 | SMD | http://www.mouser.com/ds/2/216/AP1608SGC-29521.pdf
25 | 2 | D2 | OSRAM Opto | LB Q39G-L2OO-35-1 | 720-LBQ39GL2N2351 | $0.15 | $0.30 | Blue LED | 0603 | SMD
26 | 2 | D3,D4 | OSRAM Opto | LS Q976-NR-1 | 720-LSQ976-NR-1 | $0.10 | $0.20 | Red LED | 0603 | SMD | http://www.mouser.com/ds/2/311/LS%20Q976%20-%20CHIPLED%200603-741036.pdf
28 | 4 | D5,D6 | Rectron | FM5819-W | 583-FM5819 | $0.15 | $0.60 | relay diode | DO-214AC | SMD
29 | 4 | D106,D108 | Diodes Incorportated | BZT52C16-7-F | 621-BZT52C16-F | $0.19 | $0.76 |  |  | SMD
30 | 2 | D109 | ON Semicondutor | BAV99WT1G | 863-BAV99WT1G | $0.00 | $0.00 |  |  | SMD
31 | 2 | L102 | Laird Technologies | TYS50402R2N-10 | 875-TYS50402R2N-10 | $0.38 | $0.76 | 2.2uH Inductor |  | SMD
32 | 2 | L103 | Taiyo Yuden | NRS8030T3R3MJGJ | 963-NRS8030T3R3MJGJ | $0.48 | $0.96 | 3.3uH Inductor | 8030 | SMD
33 | 2 | D110 | Diodes Incorportated | B340-13-F | 621-B340-F | $0.34 | $0.68 | input diode |  | SMD
34 | 2 | F101 | Bourns | MF-LSMF260X-2 | 652-MF-LSMF260X-2 | $0.46 | $0.92 | Resetable fuse | 3121 | SMD
35 | 4 | K1,K2 | Omron Electronics | G5LE-1A4 DC3 | Z3697-ND | $1.43 | $5.72 | 10A Relay |  | Thru Hole |  | DIGIKEY
36 | 2 | P1 | JAE Electronics | DX4R005JJ6R1500 | 656-DX4R005JJ6R1500 | $0.97 | $1.94 | MicroB USB connector |  | Thru Hole
37 | 2 | P2 |  |  |  |  | $0.00
38 | 8 | P3,P4,P5,P6 | JST (Sparkfun) |  | PRT-09916 | $1.50 | $12.00 | JST PH 4 pin (full assembly) | CONN | Thru Hole | https://www.sparkfun.com/products/9916
39 | 14 | P7,P8,P9,P10,P11,P12,P13 | Molex | 172310-1102 | 538-172310-1102 | $0.72 | $10.08 | UltraFit 2pin Header(male) | CONN | Thru Hole
40 | 8 | R1,R9,R10,R11 | Panasonic | ERJ-3EKF1001V | 667-ERJ-3EKF1001V | $0.10 | $0.80 | 1k ohm resistor | 0603 | SMD | http://www.mouser.com/ds/2/315/AOA0000CE2-37512.pdf | order 100
41 | 36 | R2,R12,R13,R18,R29,R30,R31,R34,R35,R36,R37,R38,R109,R126,R130,R140,R141,R145 | Panasonic | ERJ-3GEYJ103V | 667-ERJ-3GEYJ103V | $0.10 | $3.60 | 10k ohm resistor | 0603 | SMD |  | order 100
42 | 4 | R3,R4 | Vishay / Dale | CRCW060333R0FKEA | 71-CRCW0603-33-E3 | $0.10 | $0.40 | 33 ohm resistor | 0603 | SMD
43 | 6 | R14,R15,R16 | Susumu | RR0816P-123-D | 754-RR0816P-123D | $0.10 | $0.60 | 12k ohm resistor (0.5%) | 0603 | SMD | http://www.mouser.com/ds/2/392/susumu_RR_Data_Sheet-358748.pdf
44 | 2 | R17 | KOA Speer | RK73B1JTTDD241J | 660-RK73B1JTTDD241J | $0.08 | $0.16 | 240 ohm resistor | 0603 | SMD | http://www.mouser.com/ds/2/219/RK73B-919.pdf
45 | 10 | R5,R6,R7,R8,R28 | Panasonic | ERJ-3EKF4701V | 667-ERJ-3EKF4701V | $0.10 | $1.00 | 4.7k ohm resistor | 0603 | SMD | http://www.mouser.com/ds/2/315/AOA0000CE2-37512.pdf | order 100
46 | 4 | R32,R33 | KOA Speer | RK73B1JTTDD121J | 660-RK73B1JTTDD121J | $0.08 | $0.32 | 120 ohm resistor | 0603 | SMD | http://www.mouser.com/ds/2/219/RK73B-919.pdf
47 | 4 | R108,R146 | Panasonic | ERJ-3EKF3322V | 667-ERJ-3EKF3322V | $0.10 | $0.40 | 33.2k ohm resistor | 0603 | SMD | http://www.mouser.com/ds/2/427/dcrcwe3-109170.pdf
48 | 2 | R147 | Panasonic | ERJ-3EKF5622V | 667-ERJ-3EKF5622V | $0.10 | $0.20 | 56.2k ohm resistor | 0603 | SMD | http://www.mouser.com/ds/2/315/AOA0000CE2-37512.pdf
49 | 4 | R148, R150 | Panasonic | ERJ-3EKF10R0V | 667-ERJ-3EKF10R0V | $0.10 | $0.40 | 10 ohm resistor | 0603 | SMD | http://www.mouser.com/ds/2/315/AOA0000CE2-37512.pdf
50 | 2 | R149 | Bourns | CR0603-FX-2742ELF | 652-CR0603FX-2742ELF | $0.10 | $0.20 | 27.4K ohm resistor | 0603 | SMD | http://www.mouser.com/ds/2/54/hpreztr-777398.pdf
51 | 2 | R151 | Panasonic | ERJ-3EKF1022V | 667-ERJ-3EKF1022V | $0.10 | $0.20 | 10.2k ohm resistor | 0603 | SMD | http://www.mouser.com/ds/2/315/AOA0000CE2-37512.pdf
52 | 2 | R152 | Vishay | RCA0603100KJNEC | 71-RCA0603100KJNEC | $0.09 | $0.18 | 100k ohm resistor | 0603 | SMD | http://www.mouser.com/ds/2/427/rcae3-515375.pdf
53 | 16 | C1,C2,C3,C4,C18,C19,C21,C2 | Wurth Electronics | 885012106017 | 710-885012106017 | $0.08 | $1.28 | 1uF capacitor | 0603 | SMD
54 | 2 | C5 | Yageo | CC0603MRX5R5BB225 | 603-CC603MRX5R5BB225 | $0.10 | $0.20 | 2.2uF capacitor | 0603 | SMD | http://www.mouser.com/ds/2/447/UPY-GPHC_X5R_4V-to-50V_14_0717-202131.pdf
55 | 16 | C6,C9,C10,C11,C13,C15, C19,C121 | Wurth Electronics | 885012206071 | 710-885012206071 | $0.04 | $0.64 | 100nF capacitor (0.1uf) | 0603 | SMD
56 | 2 | C109 | Wurth Electronics | 885012105016 | 710-885012105016 | $0.02 | $0.04 | 100nF capacitor | 0402 | SMD | http://www.mouser.com/ds/2/445/885012105016-611018.pdf
57 | 2 | C12 | Wurth Electronics | 885012206040 | 710-885012206040 | $0.04 | $0.08 | 10nF capacitor (0.01uf) | 0603 | SMD | http://www.mouser.com/ds/2/445/885012206040-555095.pdf
58 | 2 | C14 | Yageo | CC0603KRX5R5BB475 | 603-CC603KRX5R5BB475 | $0.11 | $0.22 | 4.7uF capacitor | 0603 | SMD
59 | 4 | C16,C20 | Murata Electronics | GRM188R61A106KE69D | 81-GRM188R61A106KE9D | $0.20 | $0.80 | 10uF capacitor | 0603 | SMD | http://www.murata.com/products/catalog/pdf/c02e.pdf
60 | 4 | C105,C122 | Yageo | CC1206MKX5R5BB476 | 603-CC126MKX5R5BB476 | $0.50 | $2.00 | 47uF capacitor | 1206 | SMD
61 | 4 | C114,C118 | Murata Electronics | GRM31CR61E226ME15L | 81-GRM31CR61E226ME5L | $0.50 | $2.00 | 22uF capacitor | 1206 | SMD | http://www.murata.com/products/catalog/pdf/c02e.pdf
62 | 6 | C119,C120,C123 | Vishay / Vitramon | VJ1206Y104JXBTW1BC | 77-VJ1206Y104JXBTBC | $0.10 | $0.60 | 0.1uF capacitor (100V) | 1206 | SMD | http://www.mouser.com/ds/2/427/vjw1bcbascomseries-223529.pdf
63 | 14 |  | Molex | 172256-1102 | 538-172256-1102 | $0.31 | $4.34 | UltraFit 2pin (female) |  |  | http://www.mouser.com/ds/2/276/1722561102_CRIMP_HOUSINGS-705529.pdf
64 | 28 |  | Molex | 1722533123 | WM11561CT-ND | $0.15 | $4.26 | ultrafit contacts (20awg wire) |  |  | http://www.mouser.com/ds/2/276/1722533023_sd-587746.pdf | DIGIKEY
1 | 2 | U1 | STMicroelectronics | ST1480ABDR | 511-ST1480ABDR | $1.40 | $2.80 | RS485 Transceiver | SO-8 | SMD
2 | 2 | U2 | ON Semiconductor | NCP500SN33T1G | 863-NCP500SN33T1G | $0.64 | $1.28 | 3.3V Linear Power Regulator | TSOP-5 | SMD
3 | 2 | U3 | NXP / Freescale | MKL03Z32VFG4 | 841-MKL03Z32VFG4 | $1.24 | $2.48 | Microcontroller | QFN-16 | SMD
4 | 2 | U4 | Bosch Sensortec | BME280 | 262-BME280 | $5.66 | $11.32 | Altimeter (pressure temperature) | LGA-8 | SMD
5 | 2 | U7 | Linear Technology | LT6105IDCB#TRMPBF | LT6105IDCB#TRMPBFCT-ND | $2.84 | $5.68 | Current Sense Op Amp | 6-WFDFN | SMD |  | DIGIKEY
6 | 2 | Q1 | International Rectifier | IRLL3303PbF | 942-IRLL3303PBF | $0.86 | $1.72 | Niachrome trigger mosfet | SOT-223-4 | SMD
7 | 2 | D1 | OSRAM Opto | LB Q39G-L2OO-35-1 | 720-LBQ39GL2N2351 | $0.15 | $0.30 | Blue LED | 0603 | SMD
8 | 2 | P1 | Molex | PicoBlade_53047-0610 | 538-53047-0610 | $0.67 | $1.34 | Picoblade 6 pin | CONN | Thru Hole
9 | 2 | P2 |  |  |  |  | $0.00
10 | 2 | P3 |  |  |  |  | $0.00
11 | 2 | R1 | Panasonic | ERJ-2GEJ202X | 667-ERJ-2GEJ202X | $0.10 | $0.20 | 2k ohm resistor | 0402 | SMD
12 | 2 | R2 | Vishay / Dale | CRCW04020000Z0ED | 71-CRCW0402-0-E3 | $0.10 | $0.20 | 0 ohm resistor | 0402 | SMD
13 | 6 | R3,R16,R18 | KOA Speer | RK73B1ETTP101J | 660-RK73B1ETTP101J | $0.10 | $0.60 | 100 ohm resistor | 0402 | SMD | http://www.mouser.com/ds/2/219/RK73B-919.pdf
14 | 4 | R6,R7 | Panasonic | ERJ-2RKF4701X | 667-ERJ-2RKF4701X | $0.10 | $0.40 | 4.7k ohm resistor | 0402 | SMD | http://www.mouser.com/ds/2/315/AOA0000CE2-37512.pdf
15 | 2 | R8 | KOA Speer | RK73H1ETTP1200F | 660-RK73H1ETTP1200F | $0.10 | $0.20 | 120 ohm resistor | 0402 | SMD | http://www.mouser.com/ds/2/219/RK73H-5715.pdf
18 | 2 | R19 | Welwyn Components | LRMAM0805-R02FT5 | 756-LRMAM0805R02FT5 | $0.37 | $0.74 | .02 ohm resistor | 0805 | SMD
19 | 2 | R20 | KOA Speer | RK73H1ETTP1001F | 660-RK73H1ETTP1001F | $0.10 | $0.20 | 1k ohm resistor | 0402 | SMD | http://www.mouser.com/ds/2/219/RK73H-5715.pdf
20 | 10 | C1,C2,C5,C7,C18 | Wurth Electronics | 885012105012 | 710-885012105012 | $0.05 | $0.50 | 1uF capacitor | 0402 | SMD | http://www.mouser.com/ds/2/445/885012105012-555006.pdf
21 | 2 | C3 | Yageo | CC0603MRX5R5BB225 | 603-CC603MRX5R5BB225 | $0.10 | $0.20 | 2.2uF capacitor | 0603 | SMD
22 | 2 | C4 | Yageo | CC0603KRX5R5BB475 | 603-CC603KRX5R5BB475 | $0.11 | $0.22 | 4.7uF capacitor | 0603 | SMD
23 | 12 |  | Molex | 500588000 | WM1775CT-ND | $0.10 | $1.20 | picoblade contacts |  |  |  | DIGIKEY
24 | 2 |  | Molex | 51021-0600 | 538-51021-0600 | $0.36 | $0.72
 |  |  |  |  | Board Multiplier: | 2 | Mainboard Total:
 |  |  |  |  |  |  | $144.16
 |  |  |  |  |  |  | Balloon Total:
 |  |  |  |  |  |  | $32.30
 |  |  |  |  |  |  | Grand Total:
 |  |  |  |  |  |  | $176.46

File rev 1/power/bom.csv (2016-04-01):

Reference | Value | Footprint | Datasheet | Manufacturer PN | ManPN | Man PN
P1 | 12Vin | Pin_Headers:Pin_Header_Straight_1x02
R7 | .02 | Resistors_SMD:R_0805 |  | CRF0805-FX-R020ELF
R10 | 100 | Resistors_SMD:R_0603
R11 | 100 | Resistors_SMD:R_0603
R12 | 0 | Resistors_SMD:R_0603
R13 | 0 | Resistors_SMD:R_0603
R16 | 0 | Resistors_SMD:R_0603
R17 | 0 | Resistors_SMD:R_0603
C9 | 4.7uf | Capacitors_SMD:C_0805 |  | CC0805ZRY5V6BB475
R20 | 3.9K | Resistors_SMD:R_0603
R19 | 1K | Resistors_SMD:R_0603
R21 | 3.9K | Resistors_SMD:R_0603
R22 | 1K | Resistors_SMD:R_0603
U3 | LT6105 | Power:LT6105
R18 | 1000 | Resistors_SMD:R_0603
C7 | DNP | Capacitors_SMD:C_0603
C8 | DNP | Capacitors_SMD:C_0603
U1 | KL03-QFN24 | Housings_DFN_QFN:QFN-24-1EP_4x4mm_Pitch0.5mm | DOCUMENTATION
R9 | 0 | Resistors_SMD:R_0603
R5 | 200000 | Resistors_SMD:R_0603
R6 | 10000 | Resistors_SMD:R_0603
C3 | 1uf | Capacitors_SMD:C_0603
R14 | 80 | Resistors_SMD:R_0603
R15 | 80 | Resistors_SMD:R_0603
TH1 | THERMISTOR | Pin_Headers:Pin_Header_Straight_1x02 |  | NTCLE100E3103JB0 | NTCLE100E3103JB0
R1 | 1500 | Resistors_SMD:R_0603
C2 | 1uf | Capacitors_SMD:C_0603
C4 | 10u | Capacitors_SMD:C_0805 |  | GRM21BR61E106KA73L |  | GRM21BR61E106KA73L
C6 | 10uf | Capacitors_SMD:C_0805 |  | GRM21BR61E106KA73L
C5 | 1uf | Capacitors_SMD:C_0603
R8 | 10000 | Resistors_SMD:R_0603
P2 | TC2030-CTX | Tag-Connect:TC2030-NL_SMALL
U2 | TLV71209DBV | Housings_SOT-23_SOT-143_TSOT-6:SOT-23-5 |  | TLV70036DDCR
R44 | 4.7k | Resistors_SMD:R_0603
R45 | 4.7k | Resistors_SMD:R_0603
P9 | 12Vin2 | Power:ultraFitCONN_2
P10 | 3v3Vout | Power:ultraFitCONN_2
D4 | LED | LEDs:LED-0603
D5 | LED | LEDs:LED-0603
R53 | 0 | Resistors_SMD:R_0603
R54 | DNP | Resistors_SMD:R_0603
D11 | ZENER | Diodes_SMD:Diode-SMB_Standard |  | SMBJ16CA-E3/52
U8 | MMQA | Power:SC-74
D12 | ZENER | Diodes_SMD:Diode-SMA_Standard |  | 1SMA5.0AT3G
Q4 | Q_PMOS_GSD | Housings_SOT-23_SOT-143_TSOT-6:SOT-23 |  | DMP3099L
Q6 | Q_PMOS_GSD | Housings_SOT-23_SOT-143_TSOT-6:SOT-23 |  | DMP3099L
P5 | 3v3Out | Socket_Strips:Socket_Strip_Straight_1x01
P6 | 3v3Bypass | Socket_Strips:Socket_Strip_Straight_1x01
U5 | TPS563200 | Housings_SOT-23_SOT-143_TSOT-6:SOT-23-6
C10 | 22uf | Capacitors_SMD:C_1206 |  | GRM31CR61E226ME15L
C11 | 100nf | Capacitors_SMD:C_0402
R25 | 33.2k | Resistors_SMD:R_0603
R26 | 10k | Resistors_SMD:R_0603
L1 | 2.2uh | SMD_Packages:SMD-2010_Pol |  | TYS50402R2N-10
R24 | 10K | Resistors_SMD:R_0603
R23 | 10K | Resistors_SMD:R_0603
C12 | 47uf | Capacitors_SMD:C_1206 |  | GRM31CE70J476ME15L
Q3 | MOS_N_numbered | Housings_SOT-23_SOT-143_TSOT-6:SOT-23 |  | DMG2302U
U6 | LT3652 | Housings_DFN_QFN:DFN-12-1EP_3x3mm_Pitch0.45mm
C13 | 10uf | Capacitors_SMD:C_0805
R27 | 13.7k | Resistors_SMD:R_0603
R28 | 10k | Resistors_SMD:R_0603
C15 | 1uf | Capacitors_SMD:C_0603
L2 | 5.6uh | ASPI-6045S-5R6M-T:ASPI-6045S-5R6M-T |  | ASPI-6045S-5R6M-T
D7 | CMSH3-40MA | Diodes_SMD:Diode-SMA_Standard
C16 | 10uf | Capacitors_SMD:C_0805
R34 | .1 | Resistors_SMD:R_0805
TH2 | THERMISTOR | Pin_Headers:Pin_Header_Straight_1x02 |  | NTCLE100E3103JB0
R31 | 237k | Resistors_SMD:R_0603
R32 | 14.3k | Resistors_SMD:R_0603
R33 | 330k | Resistors_SMD:R_0603
R29 | 49.9K | Resistors_SMD:R_0603
R30 | 10k | Resistors_SMD:R_0603
C14 | .68uf | Capacitors_SMD:C_0603 |  | CL21F684ZAFNNNE
D6 | CMDSH2-4L | Diodes_SMD:SOD-323
BT2 | BATTERY | Pin_Headers:Pin_Header_Straight_1x02
BT1 | 18650Outline | 18650:18650
P3 | BAT_POS | Socket_Strips:Socket_Strip_Straight_1x01
P4 | BAT_NEG | Socket_Strips:Socket_Strip_Straight_1x01
U7 | LT4415 | Housings_DFN_QFN:DFN-16-1EP_3x5mm_Pitch0.5mm
R35 | 237K | Resistors_SMD:R_0603
R36 | 30.1K | Resistors_SMD:R_0603
R37 | 95.3K | Resistors_SMD:R_0603
R39 | 165 | Resistors_SMD:R_0603
R38 | 165 | Resistors_SMD:R_0603
R41 | 470K | Resistors_SMD:R_0603
R42 | 470K | Resistors_SMD:R_0603
C18 | 1u | Capacitors_SMD:C_0603
C17 | 1u | Capacitors_SMD:C_0603
T_RF_OUT1 | SMA | sma:SMA
T_BP_1 | CONN_02X10 | Socket_Strips:Socket_Strip_Straight_2x10
T_BP_2 | CONN_02X10 | Socket_Strips:Socket_Strip_Straight_2x10
T_GPS1 | SMA | sma:SMA
T_PICO_BLADE1 | CONN_01X08 | uclasp:uClasp8
T_SCREW_1 | CONN_01X01 | mounting_screw:mounting_screw
T_SCREW_2 | CONN_01X01 | mounting_screw:mounting_screw
T_SCREW_3 | CONN_01X01 | mounting_screw:mounting_screw
F1 | FUSE | Fuse_Holders_and_Fuses:Fuse_SMD2920 |  | MF-LSMF260X-2
D1 | DIODE | Diodes_SMD:Diode-SMA_Standard |  | B340-13-F
R2 | 10 | Resistors_SMD:R_0603
C1 | 1uf 100v | Capacitors_SMD:C_1206
Q1 | Q_PNP_BEC | Housings_SOT-23_SOT-143_TSOT-6:SOT-23 |  | MMBT3906
R3 | 100k | Resistors_SMD:R_0603
D2 | ZENER | Diodes_SMD:SOD-123 |  | BZT52C16-7-F
R4 | 27.4k | Resistors_SMD:R_0603
C19 | 1uf 100v | Capacitors_SMD:C_1206
R47 | 10 | Resistors_SMD:R_0603
C20 | .1uf 100v | Capacitors_SMD:C_1206
R48 | 10.2k | Resistors_SMD:R_0603
D10 | D_Schottky_x2_Serial_AKC | Transistors_SMD:sc70 |  | BAV99WT1G
R46 | 33.2k | Resistors_SMD:R_0603
D3 | ZENER | Diodes_SMD:SOD-123 |  | BZT52C16-7-F
Q2 | Si3407DV | Power:Si3407DV
U4 | TPS563200 | Housings_SOT-23_SOT-143_TSOT-6:SOT-23-6
C21 | 22uf | Capacitors_SMD:C_1206 |  | GRM31CR61E226ME15L
C22 | 100nf | Capacitors_SMD:C_0603
R51 | 56.2k | Resistors_SMD:R_0603
R52 | 10k | Resistors_SMD:R_0603
L3 | 3.3uh | NRS8030:NRS8030T3R3MJGJ |  | NRS8030T3R3MJGJ
R50 | 10K | Resistors_SMD:R_0603
R49 | 10K | Resistors_SMD:R_0603
C23 | 47uf | Capacitors_SMD:C_1206 |  | GRM31CE70J476ME15L
Q5 | MOS_N_numbered | Housings_SOT-23_SOT-143_TSOT-6:SOT-23 |  | DMG2302U

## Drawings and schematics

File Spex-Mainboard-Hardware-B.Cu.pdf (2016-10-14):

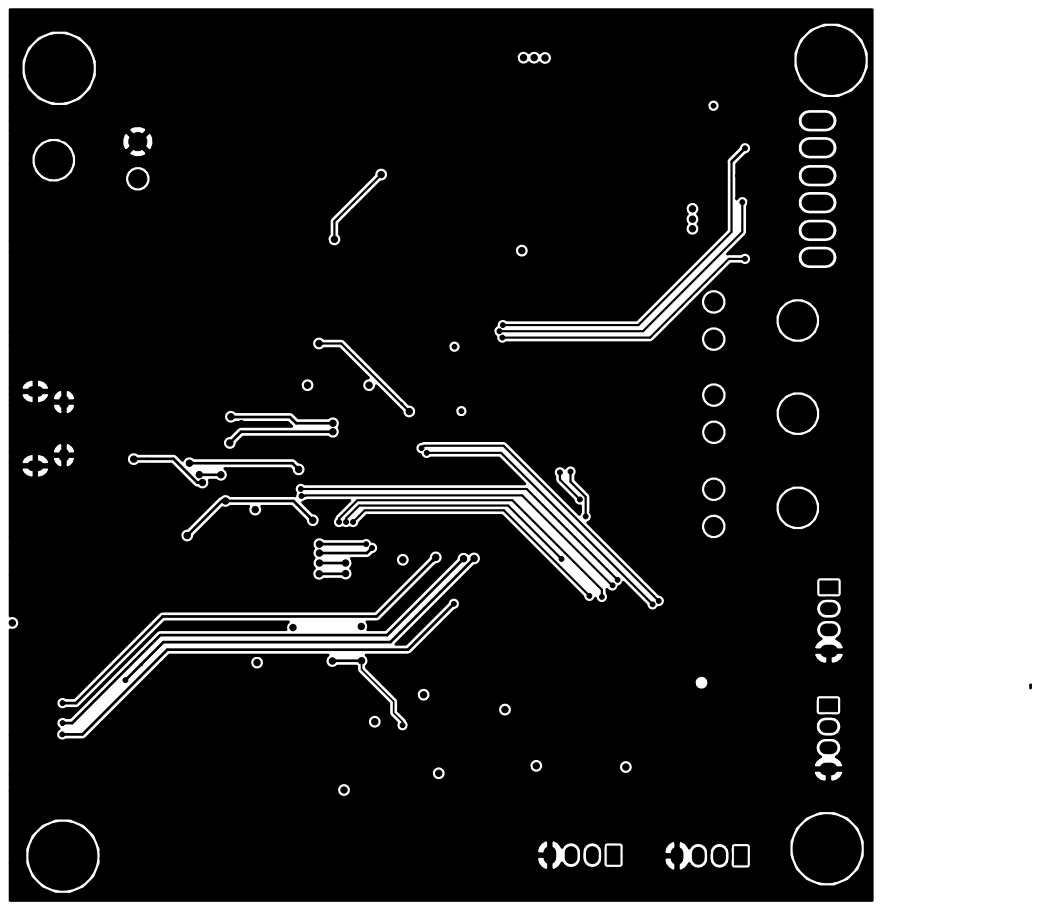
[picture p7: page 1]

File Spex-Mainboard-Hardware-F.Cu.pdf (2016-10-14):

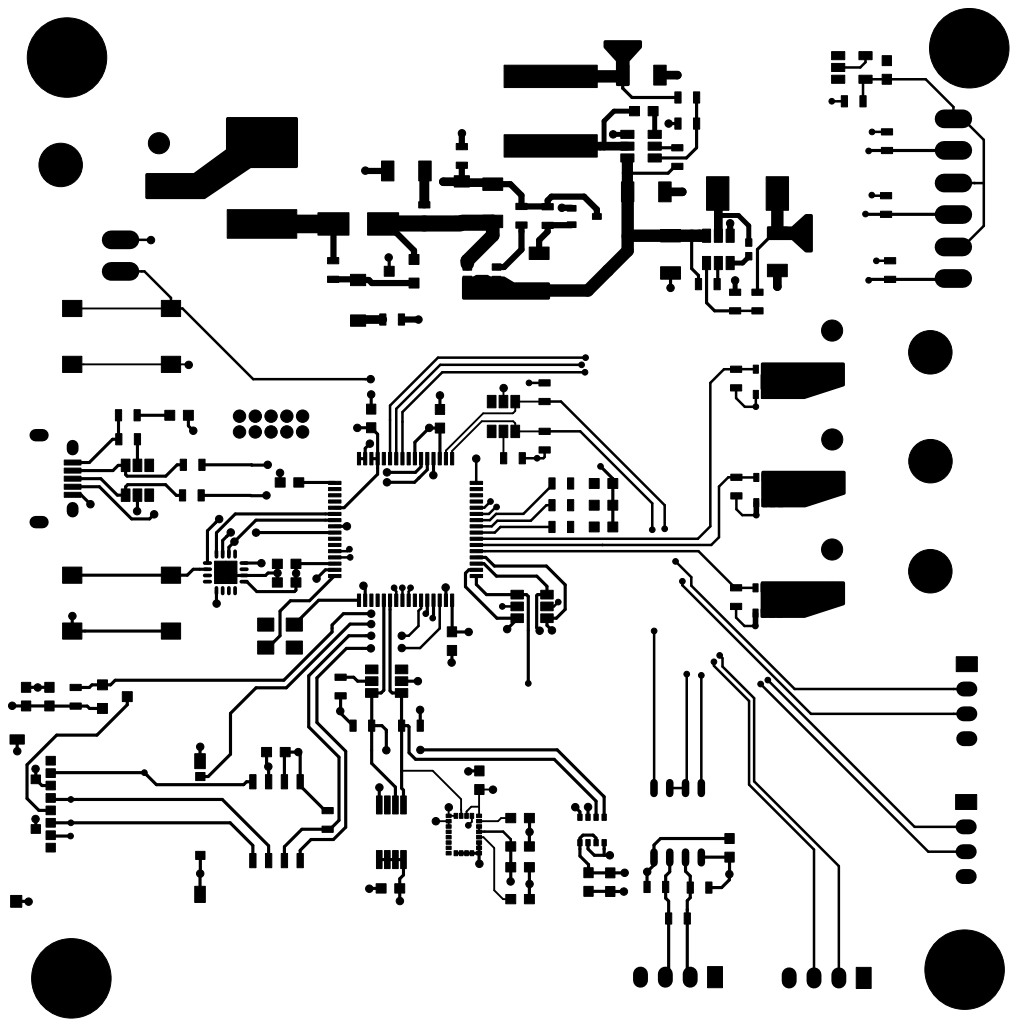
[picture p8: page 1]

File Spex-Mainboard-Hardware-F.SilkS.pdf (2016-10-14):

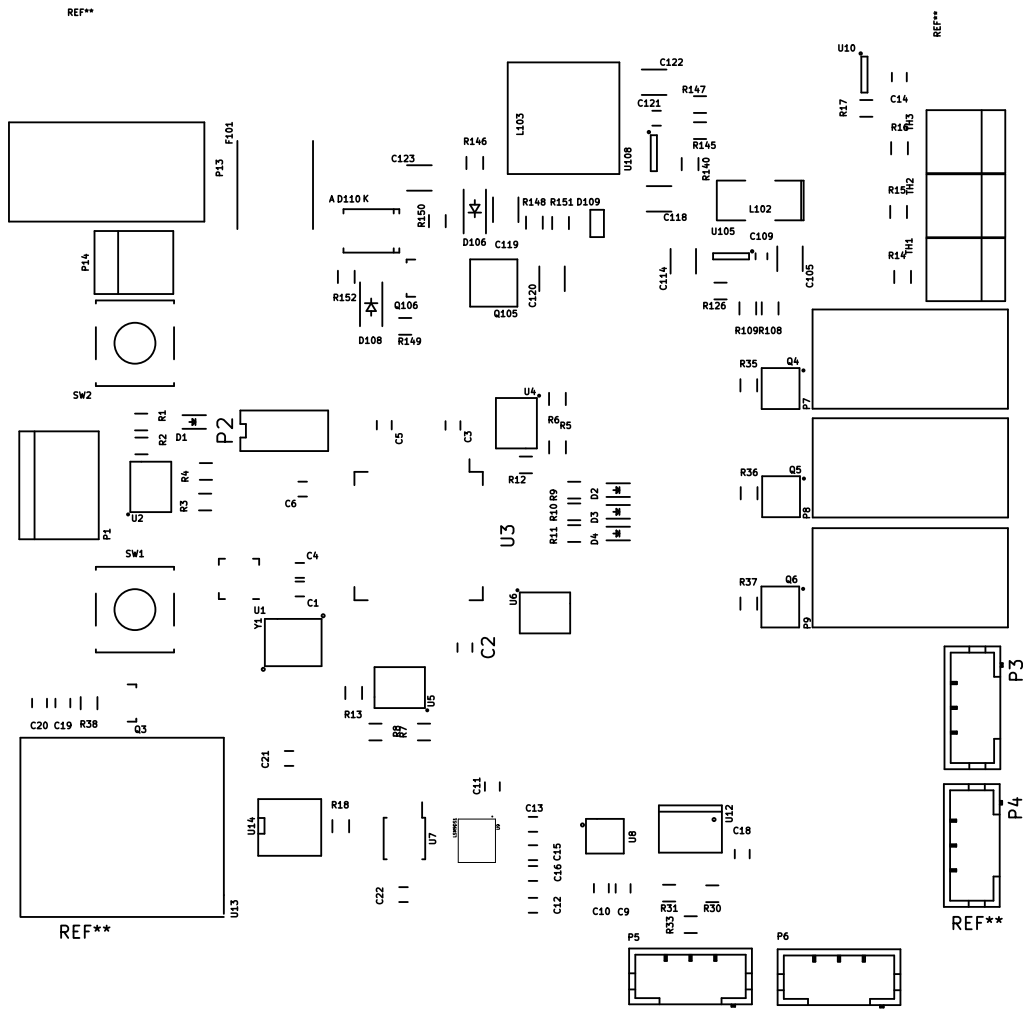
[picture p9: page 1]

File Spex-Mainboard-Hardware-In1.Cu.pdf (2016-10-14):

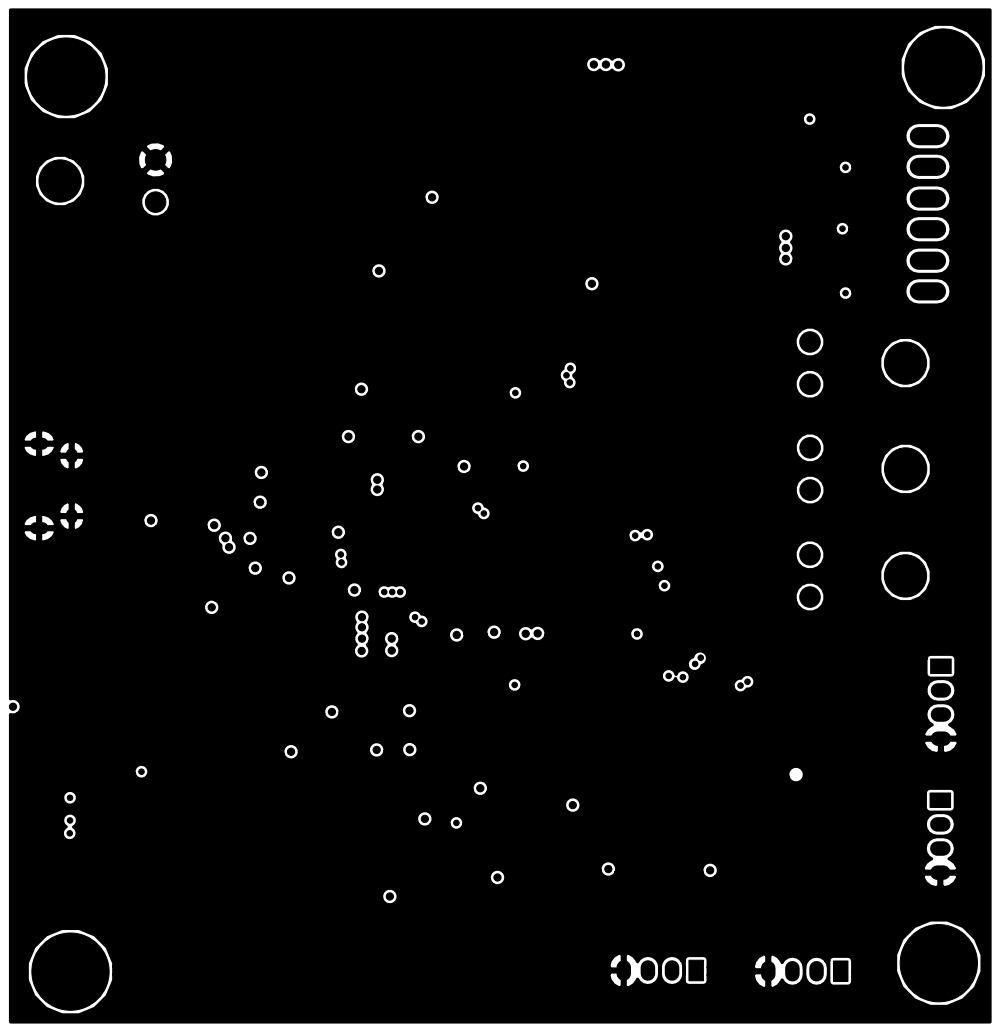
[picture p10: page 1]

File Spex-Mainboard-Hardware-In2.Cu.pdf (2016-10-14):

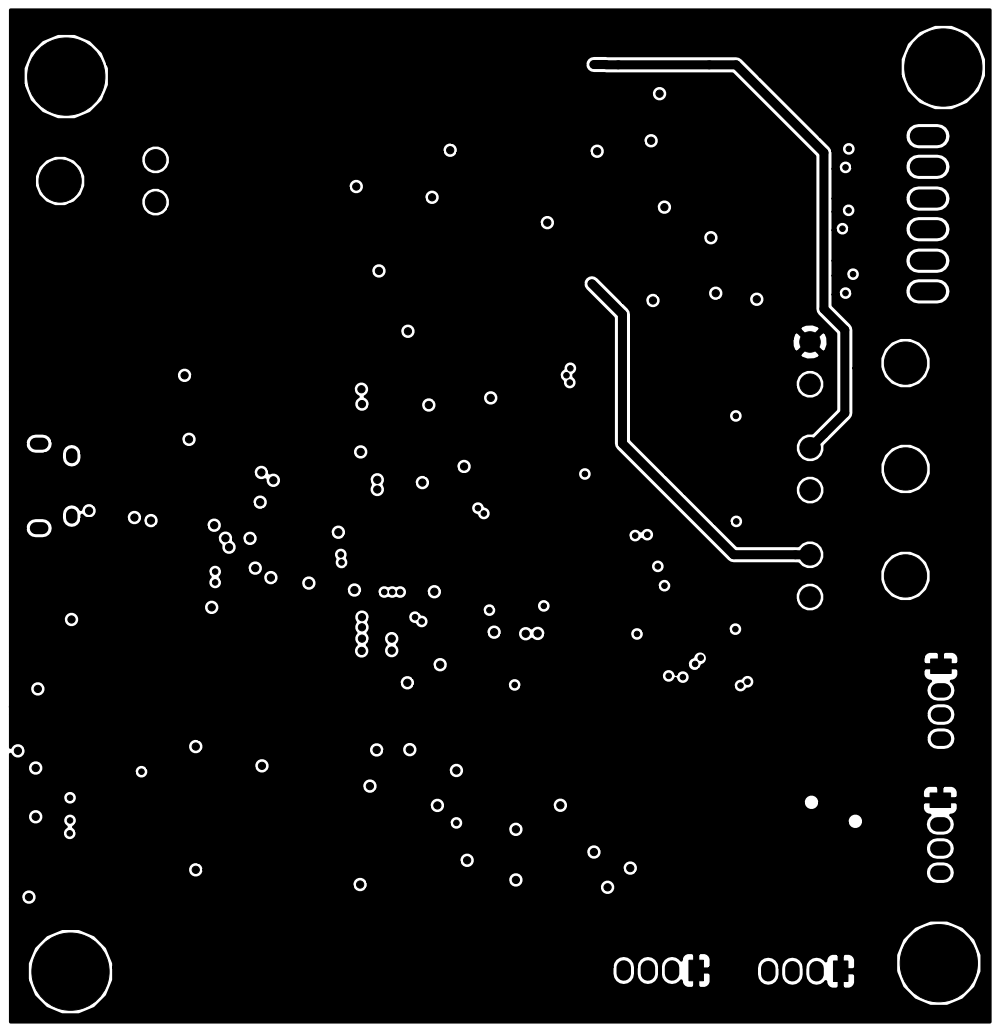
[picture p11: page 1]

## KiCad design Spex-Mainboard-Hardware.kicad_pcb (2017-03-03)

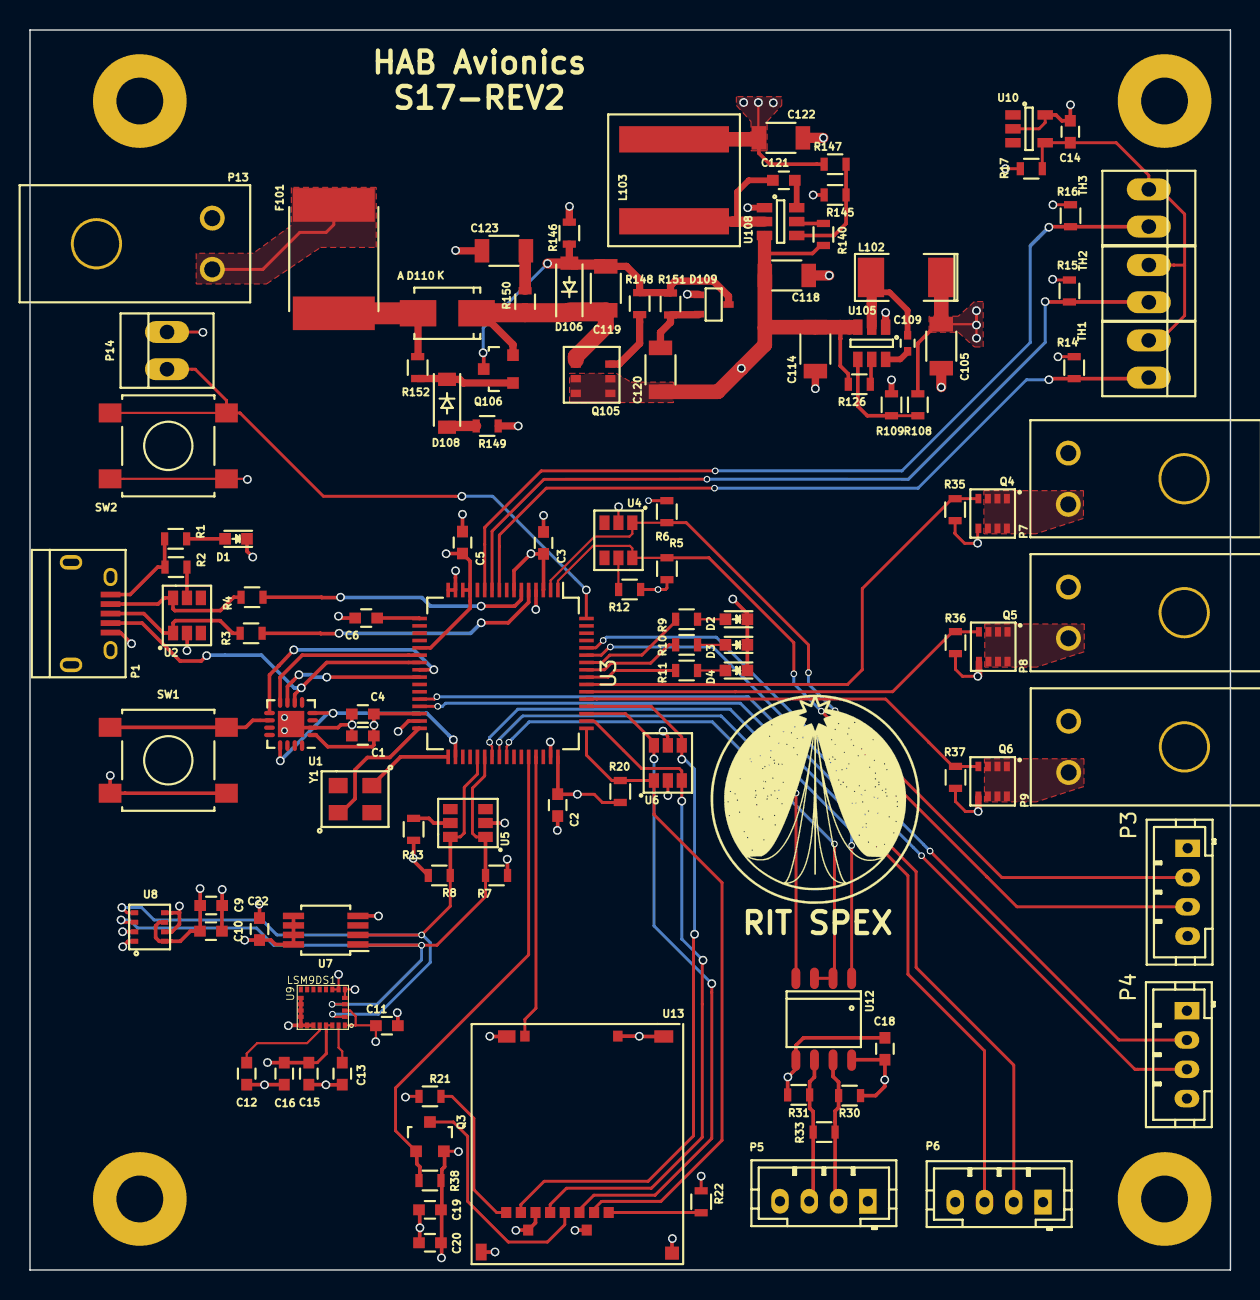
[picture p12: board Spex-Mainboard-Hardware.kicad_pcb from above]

Board: 4 copper layers, 82.0 x 84.7 mm, 113 parts (0 on the bottom side), 80 nets.

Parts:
C1, C2, C3, C4, C18, C22: 1uF; C_0603
C5: 2.2uF; C_0603
C6, C19: .1uF; C_0603
C9, C10, C11, C13, C15: 100nF; C_0603
C12: 10nF; C_0603
C14: 4.7uF; C_0603
C16, C20: 10uF; C_0603
C105, C122: 47uf; C_1206
C109: 100nf; C_0402
C114, C118: 22uf; C_1206
C119, C123: 1uf 100v; C_1206
C120: .1uf 100v; C_1206
C121: 100nf; C_0603
D1, D2, D3, D4: LED; LED_0603
D106, D108: ZENER; SOD-123
D109: D_Schottky_x2_Serial_AKC; SC-70
D110: DIODE; SMA_Standard
F101: FUSE; Fuse_SMD2920
L102: 2.2uh; SMD-2010_Pol
L103: 3.3uh; NRS8030T3R3MJGJ
P1: USB_OTG; USB_Micro-B
P3, P4, P5, P6: CONN_01X04; JST_PH_B4B-PH-K_04x2.00mm_Straight
P7, P8, P9, P13: CONN_01X02; ultraFitCONN_2
P14: CONN_01X02; PINHEAD1-2
Q3: BSS215PH6327; SOT-23
Q4, Q5, Q6: Si5468DC; ChipFet-8
Q105: Si3407DV
Q106: Q_PNP_BEC; SOT-23
R1, R9, R10, R11: 1K; R_0603
R2, R12, R20, R38, R126, R140: 10K; R_0603
R3, R4: 33; R_0603
R5, R6, R7, R8: 4.7K; R_0603
R13, R30, R31, R35, R36, R37, R109, R145: 10k; R_0603
R14, R15, R16: 12k; R_0603
R17: 240; R_0603
R21, R22: 51K; R_0603
R33: 120; R_0603
R108, R146: 33.2k; R_0603
R147: 56.2k; R_0603
R148, R150: 10; R_0603
R149: 27.4k; R_0603
R151: 10.2k; R_0603
R152: 100k; R_0603
SW1, SW2: SW_PUSH; SW_SPST_B3S-1000
TH1, TH2, TH3: THERMISTOR; PINHEAD1-2
U1: MKL02Z32VFG4; QFN-16-1EP_3x3mm_Pitch0.5mm
U2, U4, U5: NUP2201MR6; TSOP-6
U3: MK20DX256VLH7; LQFP-64_10x10mm_Pitch0.5mm
U6: MMQA6V2T1G; TSOP-6
U7: MCP9808T; MSOP-8_3x3mm_Pitch0.65mm
U8: BME280; LGA-8
U9: LSM9DS1; LGA-24
U10: LM4030; SOT-23-5
U12: ST1480ABDR; SO-8
U13: SCHA4B0419; SCH4B0419
U105, U108: TPS563200; SOT-23-6
Y1: Crystal; CX3225GB16000D0HPQCC

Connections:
3.3V_MOS_CTRL: Q4.4, R35.2, U3.55
5V_MOS_CTRL: Q5.4, R36.2, U3.54
+3V3: C1.1, C2.1, C3.1, C4.1, C5.1, C9.1, C10.1, C11.1, C15.1, C16.1, C18.1, C19.1, C20.1, C22.1, C105.1, L102.1, P3.1, P4.1, P5.1, P6.1, P7.2, Q3.2, R5.2, R6.2, R7.2, R8.2, R12.1, R13.1, R17.1, R20.1, R21.1, R22.2, R30.1, R38.2, R108.1, U1.1, U3.3, U3.7, U3.13, U3.14, U3.21, U3.30, U3.48, U7.5, U7.6, U7.7, U7.8, U8.2, U8.6, U8.8, U9.1, U9.3, U9.7, U9.8, U9.22, U9.23, U12.8
+5V: C122.1, L103.1, P8.2, R147.1
/Data_Input_Output/3.3V_MOS_OUT: P7.1, Q4.1, Q4.2, Q4.3, Q4.6, Q4.7, Q4.8
/Data_Input_Output/5V_MOS_OUT: P8.1, Q5.1, Q5.2, Q5.3, Q5.6, Q5.7, Q5.8
/Data_Input_Output/RS485_A: P5.3, R31.1, R33.2, U12.6
/Data_Input_Output/RS485_B: P5.2, R30.2, R33.1, U12.7
/Data_Input_Output/Vbus_MOS_OUT: P9.1, Q6.1, Q6.2, Q6.3, Q6.6, Q6.7, Q6.8
/HAB Sensors/2.5VRefVoltage: C14.1, R17.2, TH1.1, TH2.1, TH3.1, U10.4
/PTA6: P1.4, U1.6, U3.23
/PTA7: U1.7, U3.25
/PTB0: U1.8, U3.22
/PTB1: U1.9, U3.24
/PTB2: SW1.1, U1.10
/Power Distribution/VBat: F101.1, P13.2
/Toggle: P14.1, SW2.1, U3.64
GND: C1.2, C2.2, C3.2, C4.2, C5.2, C6.2, C9.2, C10.2, C11.2, C12.2, C13.2, C14.2, C15.2, C16.2, C18.2, C19.2, C20.2, C22.2, C105.2, C114.1, C118.1, C122.2, C123.2, D1.1, D2.1, D3.1, D4.1, D109.1, P1.5, P1.6, P3.4, P4.4, P5.4, P6.4, P13.1, P14.2, Q4.5, Q5.5, Q6.5, R14.2, R15.2, R16.2, R31.2, R35.1, R36.1, R37.1, R109.2, R145.2, R146.2, R149.2, SW1.2, SW2.2, U1.2, U2.2, U3.4, U3.15, U3.16, U3.31, U3.47, U4.2, U5.2, U6.2, U6.5, U7.4, U8.1, U8.5, U8.7, U9.5, U9.6, U9.14, U9.15, U9.16, U9.17, U9.18, U9.19, U9.20, U10.2, U10.5, U12.5, U13.6, U13.10, U105.1, U108.1
I2C0_SCL: R8.1, U3.37, U5.6, U7.2, U8.4, U9.2
I2C0_SDA: R7.1, U3.38, U5.1, U7.1, U8.3, U9.4
I2C1_SCL: P3.2, R6.1, U3.2, U4.1
I2C1_SDA: P3.3, R5.1, U3.1, U4.6
I/O-1: P6.2, U3.28
I/O-2: P6.3, U3.29
LED_Heartbeat: R9.1, U3.58
LED_Status_1: R10.1, U3.57
LED_Status_2: R11.1, U3.56
unnamed: C6.1, U3.17
unnamed: C12.1, U9.21
unnamed: C13.1, U9.24
unnamed: C109.1, L102.2, U105.2
unnamed: C109.2, U105.6
unnamed: C119.1, D106.1, D110.1, Q105.4, Q106.2, R150.1
unnamed: C119.2, D106.2, D109.3, Q106.3, R146.1, R148.2, R151.2
unnamed: C120.2, D109.2, R151.1
unnamed: C121.1, L103.2, U108.2
unnamed: C121.2, U108.6
unnamed: C123.1, R150.2
unnamed: D1.2, R1.2
unnamed: D2.2, R9.2
unnamed: D3.2, R10.2
unnamed: D4.2, R11.2
unnamed: D108.1, Q106.1, R152.1
unnamed: D108.2, R149.1
unnamed: D110.2, F101.2, R152.2
unnamed: P1.1, R1.1, R2.2
unnamed: P1.2, R4.2, U2.6
unnamed: P1.3, R3.2, U2.1
unnamed: Q3.3, U13.4
unnamed: Q105.3, R148.1
unnamed: R2.1, U2.5
unnamed: R3.1, U3.5
unnamed: R4.1, U3.6
unnamed: R12.2, U4.5
unnamed: R13.2, U5.5
unnamed: R21.2, U13.8
unnamed: R22.1, U13.1
unnamed: R108.2, R109.1, U105.4
unnamed: R126.1, U105.5
unnamed: R140.1, U108.5
unnamed: R145.1, R147.2, U108.4
unnamed: U3.32, Y1.1
unnamed: U3.33, Y1.2
RESET_b: U1.4, U1.13, U3.34
RX/TX_CTRL: U3.41, U12.2, U12.3
SD_CTRL: Q3.1, R38.1, U3.44
SD_Detect: U3.45, U13.9
SPI0_CS0: R20.2, U3.49, U6.1, U13.2
SPI0_MISO: U3.52, U6.4, U13.7
SPI0_MOSI: U3.51, U6.6, U13.3
SPI0_SCK: U3.50, U6.3, U13.5
Temp1: R14.1, TH1.2, U3.9
Temp2: R15.1, TH2.2, U3.10
Temp3: R16.1, TH3.2, U3.11
UART0_RX: U3.39, U12.1
UART0_TX: U3.40, U12.4
UART2_RX: P4.3, U3.59
UART2_TX: P4.2, U3.60
Vbus: C114.2, C118.2, C120.1, P9.2, Q105.1, Q105.2, Q105.5, Q105.6, R126.2, R140.2, U105.3, U108.3
Vbus_MOS_CTRL: Q6.4, R37.2, U3.53

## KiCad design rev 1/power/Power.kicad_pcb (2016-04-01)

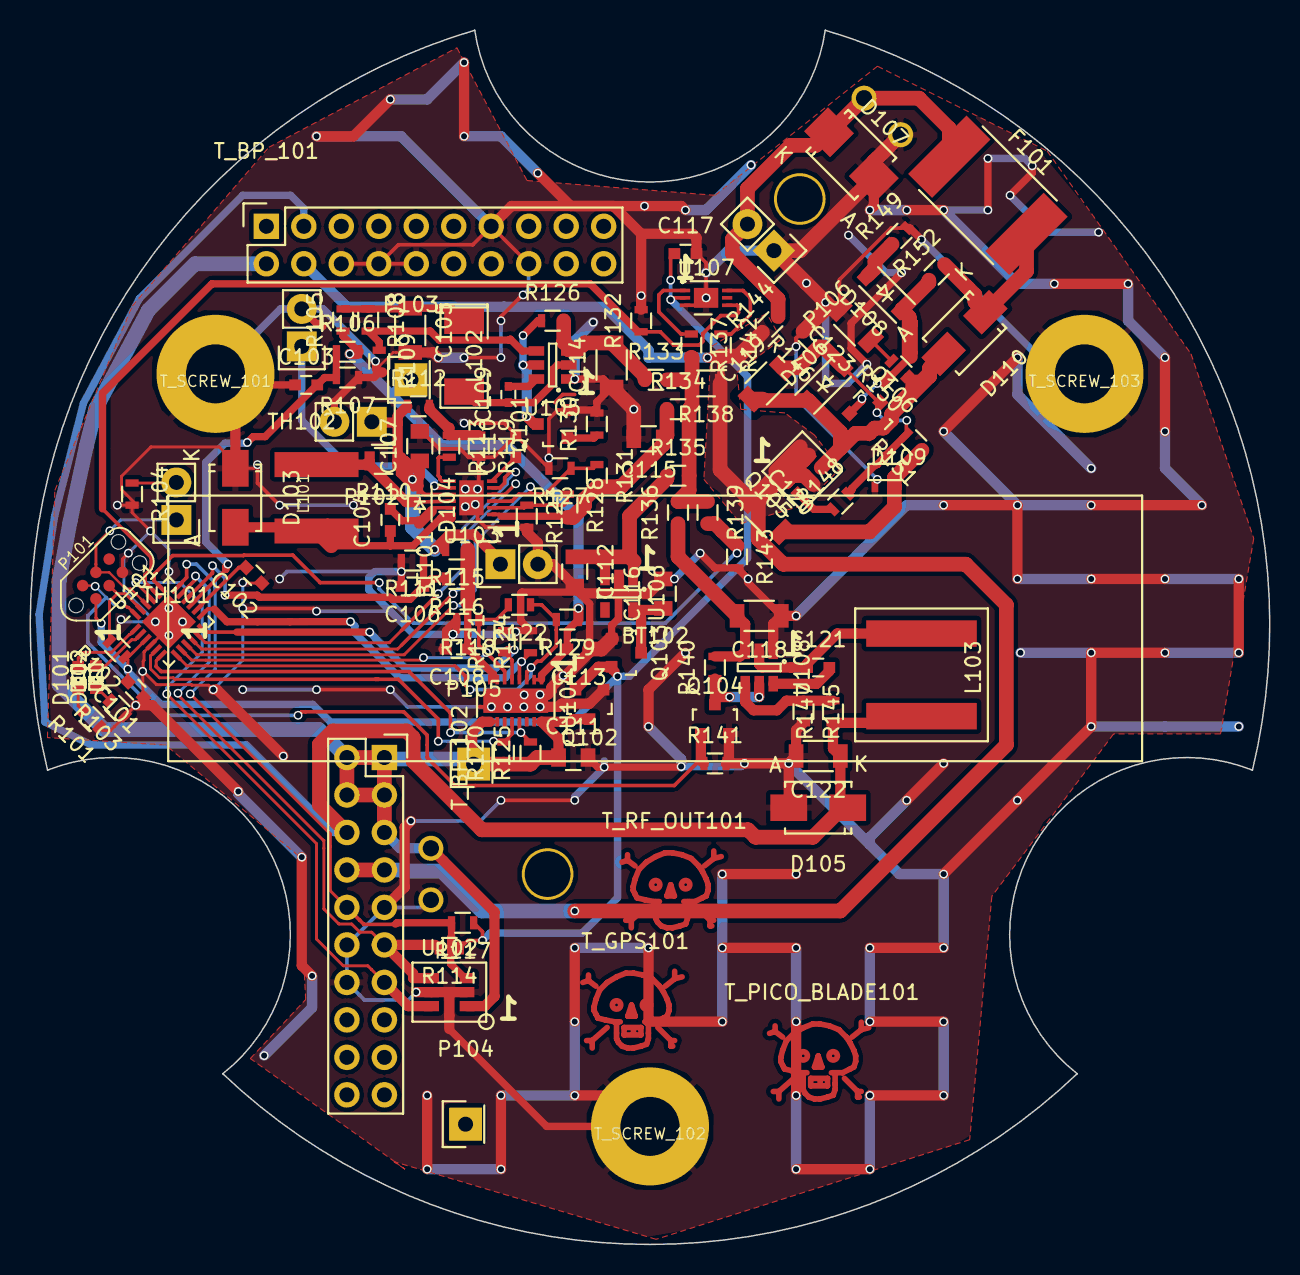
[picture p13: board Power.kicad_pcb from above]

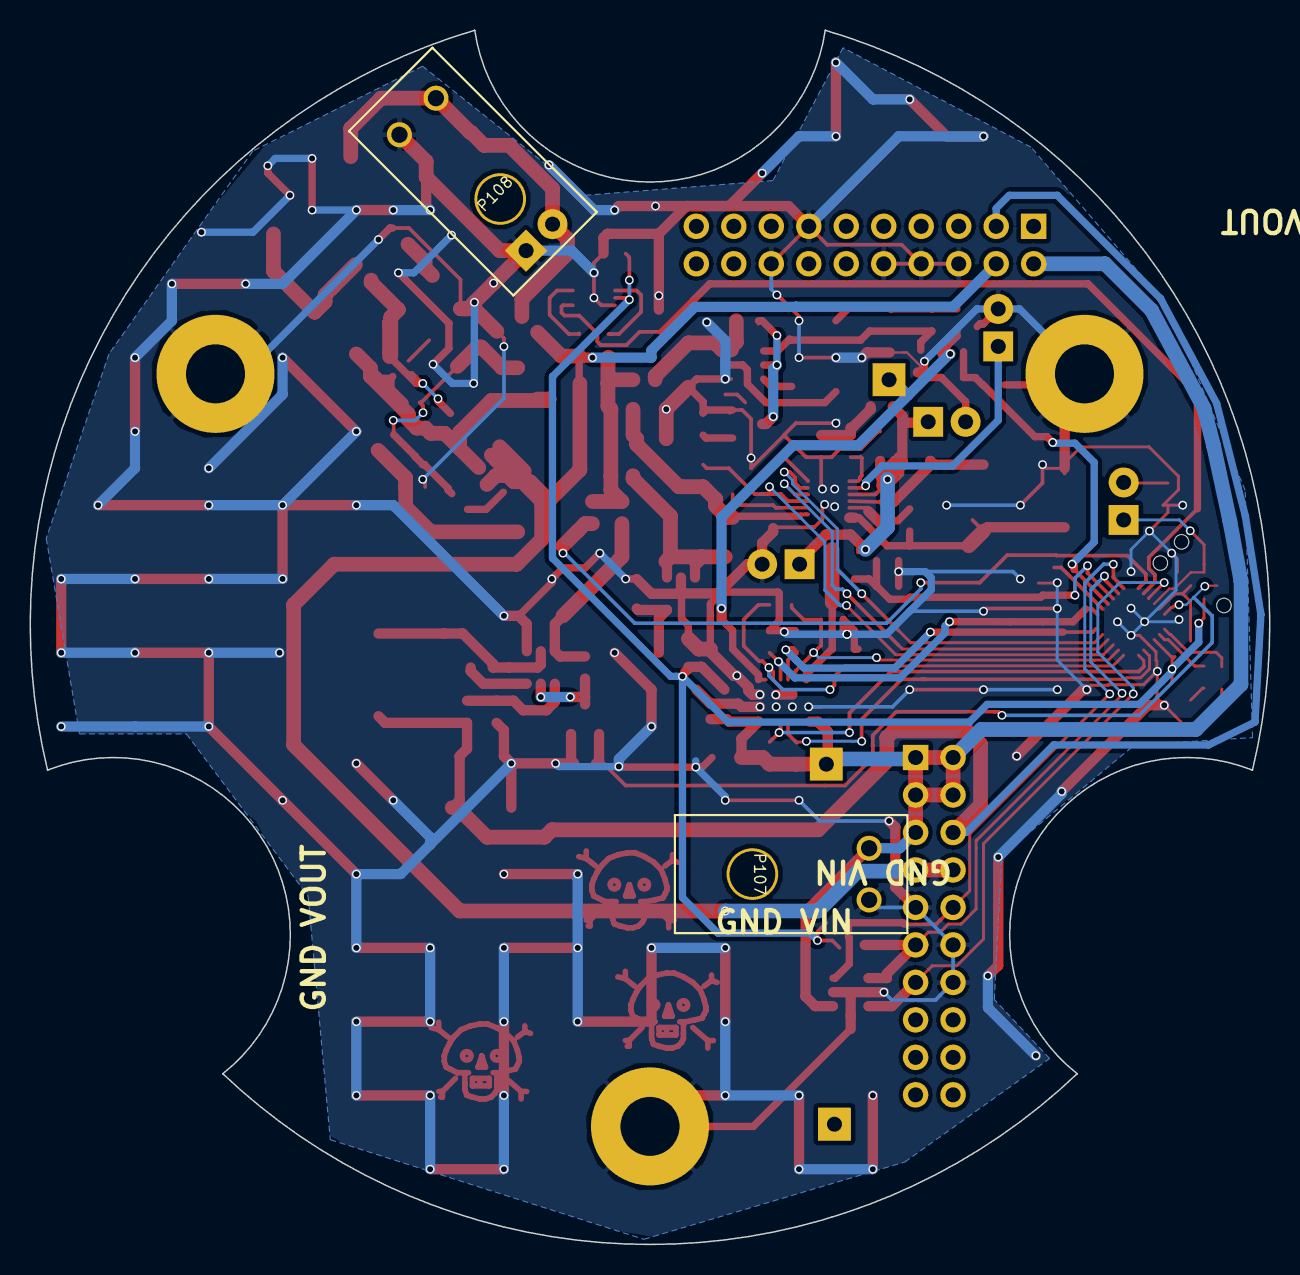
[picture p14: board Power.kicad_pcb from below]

Board: 2 copper layers, 84.0 x 82.3 mm, 123 parts (2 on the bottom side), 68 nets.

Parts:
BT101: BATTERY; Pin_Header_Straight_1x02
BT102: 18650Outline; 18650
C101, C102, C104, C117: 1uf; C_0603
C103, C106: DNP; C_0603
C105, C122: 47uf; C_1206
C107, C115, C116: 10uf; C_0805
C108, C113: 1u; C_0603
C109: 100nf; C_0402
C110: .68uf; C_0603
C111: 4.7uf; C_0805
C112: 10u; C_0805
C114, C118: 22uf; C_1206
C119, C123: 1uf 100v; C_1206
C120: .1uf 100v; C_1206
C121: 100nf; C_0603
D101, D102: LED; LED-0603
D103: CMSH3-40MA; Diode-SMA_Standard
D104: CMDSH2-4L; SOD-323
D105: ZENER; Diode-SMA_Standard
D106, D108: ZENER; SOD-123
D107: ZENER; Diode-SMB_Standard
D109: D_Schottky_x2_Serial_AKC; sc70
D110: DIODE; Diode-SMA_Standard
F101: FUSE; Fuse_SMD2920
L101: 5.6uh; ASPI-6045S-5R6M-T
L102: 2.2uh; SMD-2010_Pol
L103: 3.3uh; NRS8030T3R3MJGJ
P101: TC2030-CTX; TC2030-NL_SMALL
P102: BAT_POS; Socket_Strip_Straight_1x02
P103: 3v3Out; Socket_Strip_Straight_1x01
P104: BAT_NEG; Socket_Strip_Straight_1x01
P105: 3v3Bypass; Socket_Strip_Straight_1x01
P106: 12Vin; Pin_Header_Straight_1x02
P107: 3v3Vout; ultraFitCONN_2
P108: 12Vin2; ultraFitCONN_2
Q101, Q104: MOS_N_numbered; SOT-23
Q102, Q103: Q_PMOS_GSD; SOT-23
Q105: Si3407DV
Q106: Q_PNP_BEC; SOT-23
R101, R103: 80; R_0603
R102, R143: 10000; R_0603
R104: 1500; R_0603
R105, R115, R133, R134, R135, R136: 0; R_0603
R106, R116: 3.9K; R_0603
R107, R111: 1K; R_0603
R108, R146: 33.2k; R_0603
R109, R123, R127, R145: 10k; R_0603
R110: .1; R_0805
R112: 14.3k; R_0603
R113: 237k; R_0603
R114, R117: 4.7k; R_0603
R118: 95.3K; R_0603
R119: 330k; R_0603
R120, R125: 470K; R_0603
R121, R124: 165; R_0603
R122: 30.1K; R_0603
R126, R130, R140, R141: 10K; R_0603
R128: 13.7k; R_0603
R129: 237K; R_0603
R131: 49.9K; R_0603
R132: 1000; R_0603
R137, R142: 100; R_0603
R138: .02; R_0805
R139: 200000; R_0603
R144: DNP; R_0603
R147: 56.2k; R_0603
R148, R150: 10; R_0603
R149: 27.4k; R_0603
R151: 10.2k; R_0603
R152: 100k; R_0603
TH101, TH102: THERMISTOR; Pin_Header_Straight_1x02
T_BP_101, T_BP_102: CONN_02X10; Socket_Strip_Straight_2x10
T_GPS101: SMA; Symbol_Danger_CopperTop_Small
T_PICO_BLADE101: CONN_01X08; Symbol_Danger_CopperTop_Small
T_RF_OUT101: SMA; Symbol_Danger_CopperTop_Small
T_SCREW_101, T_SCREW_102, T_SCREW_103: CONN_01X01; mounting_screw
U101: KL03-QFN24; QFN-24-1EP_4x4mm_Pitch0.5mm
U102: MMQA; SC-74
U103: LT3652; DFN-12-1EP_3x3mm_Pitch0.45mm
U104: LT4415; DFN-16-1EP_3x5mm_Pitch0.5mm
U105, U108: TPS563200; SOT-23-6
U106: TLV71209DBV; SOT-23-5
U107: LT6105

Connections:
/12Vto3v3/En: Q101.1, R130.1
/12Vto3v3/Vin: C114.2, R126.2, R133.1, U105.3
/12Vto3v3/Vout: C105.1, L102.1, R105.2, R108.1
/12Vto5V/En: P101.2, Q104.1, R141.1, U101.24
/12Vto5V/Vin: C118.2, R136.1, R140.2, U108.3
/BatVOut: C106.1, R111.1, R116.2, U101.16
/MainCurrent: R132.1, U101.20, U107.4
/SWD_CLK: P101.4, TH101.1, U101.22
/SWD_RST: P101.3, R102.2, U101.23
/SwitchVOut: C103.2, R106.1, R107.2, U101.15
/VBackup: C101.2, C117.1, P101.1, Q102.2, Q103.2, R102.1, R114.1, R117.1, U101.3, U107.2
/VInSense: R139.2, R143.1, U101.19
/VREF: C102.2, U101.14
/dualIdealDiode/Current1: R124.1, U101.13, U104.4
/dualIdealDiode/Current2: R121.1, U101.12, U104.5
/dualIdealDiode/EN1: R122.1, R129.2, U101.7, U104.3
/dualIdealDiode/EN2: R118.1, R122.2, U101.8, U104.6
/dualIdealDiode/VIN1: C113.2, P103.1, R105.1, R106.2, R129.1, U104.1, U104.2
/dualIdealDiode/VIN2: C108.1, R115.1, R116.1, U104.7, U104.8
/dualIdealDiode/WARN1: R125.2, U101.6, U104.13
/dualIdealDiode/WARN2: R120.2, U101.5, U104.12
/lifepo4Charger/CHRG: U101.10, U103.4
/lifepo4Charger/FAULT: U101.11, U103.5
/lifepo4Charger/SHDN: R127.1, R131.1, U101.9, U103.3
/lifepo4Charger/Vin: C115.1, R128.2, R131.2, R134.1, U103.1
/lifepo4Charger/Vout: BT101.1, C107.1, D104.1, P102.1, R110.1, R112.1, R115.2, U103.9
/protection/Vin: D107.1, F101.1, P106.2, P108.2, R144.2
/template/3v3: C111.1, P105.1, P107.1, Q102.3, R120.1, R125.1, T_BP_101.1, T_BP_101.2, T_BP_102.1, T_BP_102.2, T_BP_102.3, T_BP_102.4, T_BP_102.5, U102.1, U104.9, U104.10, U104.15, U104.16
/template/5v: C122.1, D105.1, L103.1, R147.1, T_BP_101.3, T_BP_102.6
/template/PSU_IRQ: T_BP_102.13, U101.21, U102.6
/template/PSU_SCL: R114.2, T_BP_102.11, U101.17, U102.4
/template/PSU_SDA: R117.2, T_BP_102.10, U101.18, U102.3
/template/VBUS: C120.1, Q105.1, Q105.2, Q105.5, Q105.6, R138.1, R142.2, R144.1, T_BP_101.4, T_BP_102.7, T_BP_102.8
GND: BT101.2, C101.1, C102.1, C103.1, C105.2, C106.2, C107.2, C108.2, C110.2, C111.2, C112.2, C113.1, C114.1, C115.2, C116.2, C117.2, C118.1, C122.2, C123.2, D103.1, D105.2, D107.2, D109.1, P101.5, P106.1, P107.2, P108.1, Q101.2, Q102.1, Q103.1, Q104.2, R101.1, R103.1, R104.2, R107.1, R109.2, R111.2, R118.2, R119.2, R121.2, R123.2, R124.2, R127.2, R130.2, R132.2, R141.2, R143.2, R145.2, R146.2, R149.2, TH102.2, T_BP_101.6, T_BP_101.8, T_BP_101.10, T_BP_101.13, T_BP_101.16, T_BP_102.9, T_BP_102.12, T_BP_102.14, T_SCREW_101.1, T_SCREW_102.1, T_SCREW_103.1, U101.4, U101.25, U102.2, U102.5, U103.13, U104.17, U105.1, U106.2, U107.3, U107.7, U108.1
unnamed: C123.1, R150.2
unnamed: C112.1, R135.1, U106.1, U106.3
unnamed: C116.1, Q103.3, U106.5
unnamed: C109.1, L102.2, U105.2
unnamed: C109.2, U105.6
unnamed: C110.1, U103.6
unnamed: C104.1, D103.2, L101.1, U103.12
unnamed: C104.2, D104.2, U103.11
unnamed: C119.1, D106.1, D110.2, Q105.4, Q106.2, R150.1
unnamed: C119.2, D106.2, D109.3, Q106.3, R146.1, R148.2, R151.2
unnamed: C120.2, D109.2, R151.1
unnamed: C121.1, L103.2, U108.2
unnamed: C121.2, U108.6
unnamed: D110.1, F101.2, R152.2
unnamed: D108.1, Q106.1, R152.1
unnamed: D108.2, R149.1
unnamed: D102.1, R103.2
unnamed: D102.2, U101.2
unnamed: D101.1, R101.2
unnamed: D101.2, U101.1
unnamed: L101.2, R110.2, U103.10
unnamed: Q105.3, R148.1
unnamed: Q101.3, R126.1, U105.5
unnamed: Q104.3, R140.1, U108.5
unnamed: R104.1, TH101.2
unnamed: R142.1, U107.6
unnamed: R137.1, U107.1
unnamed: R133.2, R134.2, R135.2, R136.2, R137.2, R138.2, R139.1
unnamed: R108.2, R109.1, U105.4
unnamed: R123.1, R128.1, U103.2
unnamed: R112.2, R113.1, R119.1
unnamed: R113.2, U103.7
unnamed: R145.1, R147.2, U108.4
unnamed: TH102.1, U103.8

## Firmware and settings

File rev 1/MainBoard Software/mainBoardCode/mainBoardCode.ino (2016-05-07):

/*RIT Space Exploration HAB2 Main Avionics Board Software
 * Author: T.J. Tarazevits(venku122)
 * Board Design: Matt Glazer, Chris Culpepper
 * Launch Date: 05/08/2016
 * repo: https://github.com/RITSpexHAB/SPEX_HAB_Mainboard_Hardware
 */

#include <Adafruit_BME280.h>

#include <Wire.h>
#include <SPI.h>
#include <SD.h>
#include <elapsedMillis.h>
#include <Adafruit_MCP9808.h>

#define RELAY_1 17
#define RELAY_2 16 //payload deployment relay

#define BLUE_LED 14
#define LED_STATUS_1 2 
#define LED_STATUS_2 30

#define SEALEVELPRESSURE_HPA (1013.25) //dependent on launch conditions
#define BME_CS 18

#define SD_CS 10
#define SD_PWRCTRL 22

elapsedMillis ledFlash, pollSensor, releasePayload; //timers in milliseconds

Adafruit_MCP9808 mcp = Adafruit_MCP9808(); //onboard temp sensor
Adafruit_BME280 bme; // I2C  Altimeter/barometer

unsigned int blinkRate = 500; // milliseconds per LED flash
unsigned int pollRate = 500; // milliseconds per sensor poll
unsigned int releaseTime = 3600000; //60 minutes = 60 * 60 * 1000
boolean ledState = LOW; // On//Off toggle
boolean payloadReleased = false; //controls deployment

//calls init
void setup() {
  Serial.begin(9600);
  delay(1000);
  Serial.println("Setup");
  delay(100);
  init();
  delay(100);
  
}
//main program loop
void loop() {
    flashLED();

    if(pollSensor > pollRate) {
      pollSensors();
      pollSensor = 0;
    }

    //if deployment time is met and relay has not been raised, deploy
    if(releasePayload>releaseTime && !payloadReleased) deployPayload();
      
    
}

//initialize state variables and sensors
//Check SD card health
bool init() {
 
  //set status LED
  pinMode(BLUE_LED, OUTPUT);
  digitalWrite(BLUE_LED, ledState);
  
  //set relay to LOW
  pinMode(RELAY_2, OUTPUT);
  digitalWrite(RELAY_2, LOW);
  
  //initialize BME280
    if(!bme.begin()) {
    Serial.println("Could not find a valid BME280 sensor, check wiring!");
  }

  //initialize MCP9808
  if (!mcp.begin(0x19)) {
    Serial.println("Couldn't find MCP9808!");
    delay(50);
  }
  
  
  //initalize SD card
  pinMode(SD_PWRCTRL, OUTPUT);
  digitalWrite(SD_PWRCTRL, LOW); // powers on SD card
  if (!SD.begin(SD_CS)) {
      Serial.println("initialization failed!");
      return false;
    }
    Serial.println("initialization done.");
  return true;
}

//reads data from each sensor and stores it to stringBuilder/SD
//Currently only Barometer is functional on board rev1
void pollSensors() {
  pollBarometer();
}

//reads pressure/temp/altitude data from the barometer
void pollBarometer() {
  Serial.print("Temperature = ");
    
    Serial.print(bme.readTemperature());
    Serial.println(" *C");

    Serial.print("Pressure = ");

    Serial.print(bme.readPressure() / 100.0F);
    Serial.println(" hPa");

    Serial.print("Approx. Altitude = ");
    Serial.print(bme.readAltitude(SEALEVELPRESSURE_HPA));
    Serial.println(" m");

    Serial.print("Humidity = ");
    Serial.print(bme.readHumidity());
    Serial.println(" %");

    Serial.println();
}

//reads temperature from the onboard thermometer
void pollTempSensor() {
  float c = mcp.readTempC();
  float f = c * 9.0 / 5.0 + 32;
  Serial.print("Temp: "); Serial.print(c); Serial.print("*C\t"); 
  Serial.print(f); Serial.println("*F");
  
  Serial.println("Shutdown MCP9808.... ");
  mcp.shutdown_wake(1); // shutdown MSP9808 - power consumption ~0.1 mikro Ampere
}

//receives data from external board
//RS485 data link to HAB plug sensors
void receiveExternalBoardData() {
  //waiting for board development
}

//triggers the external payload deployment switch
void deployPayload() {
      digitalWrite(RELAY_2, HIGH); // Nichrome wire deploys cubesat solar panels
      Serial.println("relay raised HIGH");
      payloadReleased = true;
}

//flashes leds at rate defined by blinkRate
void flashLED() {
  
   if(ledFlash>blinkRate) {
    digitalWrite(BLUE_LED, ledState);
    ledState = !ledState;
    Serial.println("LED transition");
    ledFlash = 0;
  }
}

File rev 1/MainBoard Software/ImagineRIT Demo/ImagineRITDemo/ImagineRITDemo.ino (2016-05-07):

#include <elapsedMillis.h>
#define BLUE_LED 14
#define LED_STATUS_1 2 
#define LED_STATUS_2 30

elapsedMillis blueTimer, red1Timer, red2Timer;
int blinkRate = 100;
boolean blueLED, redLED1, redLED2;
void setup() {
  blueTimer=0; blueLED = LOW;
  red1Timer=0; redLED1 = LOW;
  red2Timer=0; redLED2 = LOW;
  pinMode(BLUE_LED, OUTPUT);
  digitalWrite(BLUE_LED, blueLED);

  pinMode(LED_STATUS_1, OUTPUT);
  digitalWrite(LED_STATUS_1, redLED1);

  pinMode(LED_STATUS_2, OUTPUT);
  digitalWrite(LED_STATUS_2, redLED2);

}

void loop() {
  if(blueTimer > (blinkRate * 4)) {
    digitalWrite(BLUE_LED, blueLED);
    blueLED = !blueLED;
    Serial.println("LED transition");
    blueTimer = 0;
  }

  if(red1Timer > (blinkRate * 3)) {
    digitalWrite(LED_STATUS_1, redLED1);
    redLED1 = !redLED1;
    Serial.println("LED transition");
    red1Timer = 0;
  }

  if(red2Timer > (blinkRate * 2)) {
    digitalWrite(LED_STATUS_2, redLED2);
    redLED2 = !redLED2;
    Serial.println("LED transition");
    red2Timer = 0;
  }

}

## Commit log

2016-03-24 Initial upload to SPEX HAB repo
    [Data_Input_Output.sch, HAB_Sensors.sch, Power_Regulation.sch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]
2016-03-24 added add'l temperature sensor
    [HAB_Sensors.sch]
2016-03-24 updated SD card, changed mosfets
    [Data_Input_Output.sch]
2016-03-24 updated component numbering
    [SpexPowerBoard.sch]
2016-03-24 updated schematic
    [Spex-Mainboard-Hardware.sch]
2016-04-01 Schematics updated/components generated/PCB started
    [Data_Input_Output.sch, HAB_Sensors.sch, Spex-Mainboard-Hardware.sch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]
2016-04-01 Added power board to both sch and pcb. Will route when ready for it
    [12Vto3v3.sch, 12Vto5V.sch, Power.kicad_pcb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]
2016-04-04 working on PCB layout
    [12Vto3v3.sch, 12Vto5V.sch, Data_Input_Output.sch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]
2016-04-04 board now 80% laid out
    [Spex-Mainboard-Hardware.kicad_pcb]
2016-04-04 project updated
    [12Vto3v3.sch, 12Vto5V.sch, procection.sch]
2016-04-04 schematic updated
    [Data_Input_Output.sch, HAB_Sensors.sch]
2016-04-05 updated schematic, added headers
    [Data_Input_Output.sch, HAB_Sensors.sch]
2016-04-05 continued PCB layout, small schematic changes
    [Spex-Mainboard-Hardware.kicad_pcb, Spex-Mainboard-Hardware.sch]
2016-04-06 Added powerz
    [Data_Input_Output.sch, HAB_Sensors.sch, Spex-Mainboard-Hardware.kicad_pcb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]
2016-04-06 Routed a line.
    [Spex-Mainboard-Hardware.kicad_pcb]
2016-04-08 updated board
    [12Vto3v3.sch, 12Vto5V.sch, Data_Input_Output.sch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]
2016-04-08 board layout 95% complete
    [12Vto3v3.sch, 12Vto5V.sch, Data_Input_Output.sch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]
2016-04-08 completed first revision of the board.
    [Data_Input_Output.sch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]
2016-04-09 added images, cosmetic schematic changes
    [Spex-Mainboard-Hardware.kicad_pcb]
2016-04-09 added BOM
    [SPEX HAB2 BOM.xlsx]
2016-04-09 updated passive values
    [Data_Input_Output.sch, HAB_Sensors.sch, Spex-Mainboard-Hardware.sch]
2016-04-11 updated BOM
    [SPEX HAB2 BOM.xlsx]
2016-04-11 updated BOM, fixed footprints
    [SPEX HAB2 BOM.xlsx, Spex-Mainboard-Hardware.kicad_pcb, _saved_12Vto3v3.sch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]
2016-04-12 updated gerbers
    [Spex-Mainboard-Hardware-B.Adhes.gbr, Spex-Mainboard-Hardware-B.CrtYd.gbr, Spex-Mainboard-Hardware-B.Cu.gbr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]
2016-04-12 updated PCB
    [Spex-Mainboard-Hardware.kicad_pcb]
2016-04-25 power estimate
    [HAB2 Mainboard Power Estimate.xlsx]
2016-04-27 Added data sheets for sensors and started Arduion Project
2016-04-27 Added Mainboard Software v0.1
    -Successfully blinks heartbeat
    -raises Relay 17 to HIGH after 15s
2016-04-28 Deploys Relay and Reads onboard Barometer
2016-05-07 ImagineRIT LED Light Show
    Flashing LEDs for demonstration purposes
2016-06-06 creating revision 1 backup
    [12Vto3v3.sch, 12Vto5V.sch, Data_Input_Output.sch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]
2016-08-10 rev 2 of hab board in progress
    [12Vto3v3.sch, 12Vto5V.sch, Data_Input_Output.sch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]
2016-08-24 routing power, digital portion mostly complete
    [Spex-Mainboard-Hardware.kicad_pcb, _saved_procection.sch]
2016-08-24 continued work on power electronics
    [Spex-Mainboard-Hardware.kicad_pcb, _saved_procection.sch, procection.sch]
2016-08-24 the routing never ends
    [Spex-Mainboard-Hardware.kicad_pcb, Spex-Mainboard-Hardware.sch]
2016-08-24 finished routing all but output MOSFETS
    [Spex-Mainboard-Hardware.kicad_pcb]
2016-09-16 updates per week 1 meeting
    [Data_Input_Output.sch, HAB_Sensors.sch, Spex-Mainboard-Hardware.kicad_pcb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]
2016-10-14 added images
    [Spex-Mainboard-Hardware.kicad_pcb]
2016-10-18 small update
    getting ready to order PCB's, making sure they are good to go.
    [Data_Input_Output.sch, HAB_Sensors.sch, Spex-Mainboard-Hardware.kicad_pcb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]
2016-10-19 small update round 2
    cleaning up PCB, adding SPI CS pullup resistors
    [Data_Input_Output.sch, Spex-Mainboard-Hardware.kicad_pcb, Spex-Mainboard-Hardware.sch]
2016-10-24 fixed mounting points
    [Spex-Mainboard-Hardware.kicad_pcb]
2016-10-24 routed SPI CS pull up resistors
    [Spex-Mainboard-Hardware.kicad_pcb]
2016-12-19 BOM should be usable again for Rev2
    [SPEX HAB2 BOM.xlsx]
2016-12-19 small tweaks, BOM updated
    [12Vto3v3.sch, 12Vto5V.sch, Data_Input_Output.sch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]
2016-12-19 Continued tweaks, updated BOM again
    [Data_Input_Output.sch, HAB_Sensors.sch, SPEX HAB2 BOM.xlsx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]
2017-01-30 removed SPI Flash, minor changes, updated Kicad
    [12Vto3v3.sch, 12Vto5V.sch, Spex-Mainboard-Hardware.kicad_pcb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]
2017-02-02 Redid the entire lower part of the board (sensors/SD)
    I probably have spent too much time on this board, looks better now
    though
    [Spex-Mainboard-Hardware.kicad_pcb]
2017-02-02 RTD (read the datasheet)
    keepouts are a thing
    [Spex-Mainboard-Hardware.kicad_pcb]
2017-02-06 minor trace changes and silkscreen improvements
    [Spex-Mainboard-Hardware.kicad_pcb]
2017-02-06 made it a little bit easier to see where pin 1 goes
2017-02-09 BOM update, silkscreen update
    [SPEX HAB2 BOM.xlsx, Spex-Mainboard-Hardware.kicad_pcb]
2017-02-10 fixing BOM
    [SPEX HAB2 BOM.xlsx]
2017-03-03 last min fixes to order the board
    [Spex-Mainboard-Hardware-B.Cu.gbr, Spex-Mainboard-Hardware-B.Fab.gbr, Spex-Mainboard-Hardware-B.Mask.gbr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]
